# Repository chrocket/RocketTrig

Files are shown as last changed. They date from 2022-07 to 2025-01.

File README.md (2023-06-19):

# RocketTrig
A camera controller for photographing high poweed model rockets


This is a camera controller. Each "node" contains outputs to control one or two cameras.  Camera nodes can communicate to each others over an RF link. Two nodes make up a system, say one at the flight line and one up close to the rocket. Liftoffs can be triggered by a variety of sensors to detect lift-off, or manually via a foot switch.

Schematic, BOM, JLBPCB files and firmware are all included.
Note:  Even those some files are labelled "CameraTriggerSensorNodeOnly" they are really Camera nodes.

This is based on the Adafruit Feather M0 LoRa board (Adafruit 3178). It also works with RFM65 radio version of that board, cheaper but less range (Adafruit 3176). There is a #define to select between the two, and the frequency of operation will have to be in the range of the chip.

To build firmware, you will need Arduino IDE. I'm using ver 1.8.19.  You will need to set up the Adafruit boards in the boards manager (Add https://adafruit.github.io/arduino-board-index/package_adafruit_index.json to Additional boards URL under Preferences).  Set "Adafruit Feather M0 (SAMD21)" Under Tools/Board.

I'm using dependencies (under library manager):
CRC32 by Christopher Baker  https://github.com/bakercp/CRC32/blob/master/examples/CRC32/CRC32.ino
Requires RadioHead libs
// https://www.airspayce.com/mikem/arduino/RadioHead/index.html
// Download from Adafruit https://cdn-learn.adafruit.com/assets/assets/000/035/106/original/RadioHead-1.62.zip?1472068723
CCW MorseTX
https://github.com/ridencww/cww_MorseTx

You will likely want to change the default 915.35 MHz operating frequency. This is done by a #define.  This will deconfict different users who might want to simultaneously use the sytem.

--------------------------------------------------------------------------------------------------------------
In June 2023, I had Eureka moment. I realized that with virtuallly no changes, the RocketTrig board could be used as a wireless Launch controller and still trigger cameras.  I modified the program to work with this and later worked up a separate board "Rev 4_1" that could better meet both remote launch and remote camera trigger functions.

(Remote launch can still trigger cameras both local and remote)

Here is the Rev 4_1 board
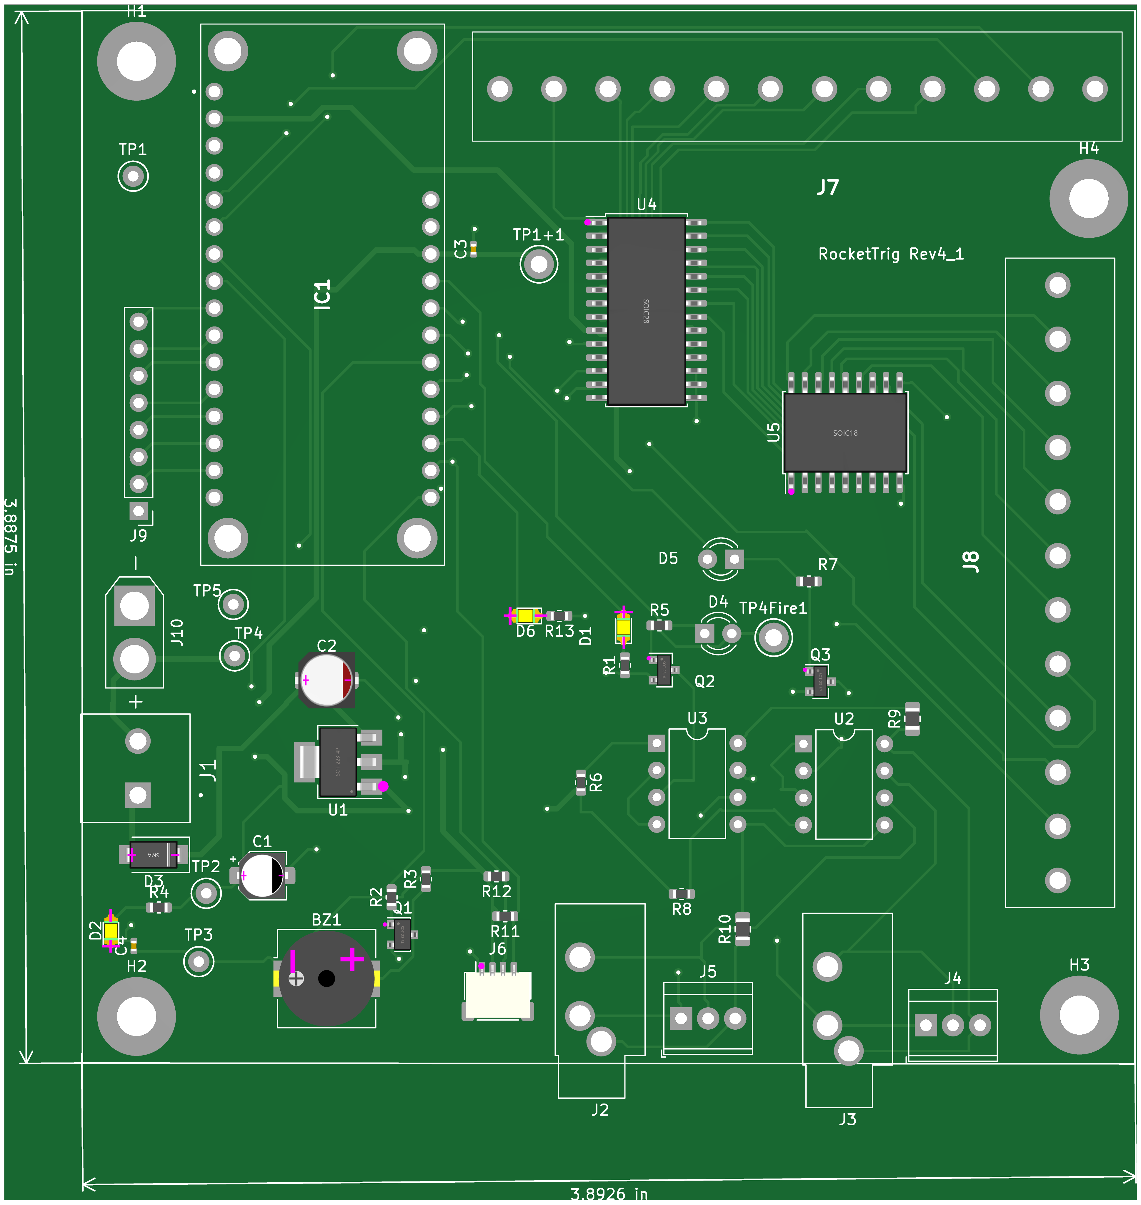
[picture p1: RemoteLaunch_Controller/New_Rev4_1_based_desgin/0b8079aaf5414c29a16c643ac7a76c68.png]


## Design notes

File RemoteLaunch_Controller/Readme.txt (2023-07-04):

Uses the CameraTrig board, as-is to create a wireless launch capability.

(Some pins for sensors are needed for a relay and LED).

Camera will trigger when "launch" is fired (for a two second "on")

Poll button becomes "clear", "Arm" is still "Arm" and "Trigger" becomes launch.

Press "Arm", which will arm system, after 15 sec, it will time out.
- Will also go to disarm, if you hit "clear"
- Will disarm after a launch.

After system is in "arm", hit "launch" to fire the ignitors in the remote box for 2s
- Hitting "clear" will turn off ignitors, if still in the 2 s window

Schematics enclosed for external board connections, as well as BOM.

***********************************************
NOTE  Variations
***********************************************
RocketTrig_based_board  is based on the orinal board   6/2023

CameraTriggerRev 4_2 w Launch Controller 2023  is a re-do with i2c i/o expander and darlington driver array  7/2023
4ChWirelessLaunchController - try 2 w relay pcb - is a relay board for Rev 4_2  7/2023

***********************************************
NOTE  Migrated to Kicad 7
***********************************************

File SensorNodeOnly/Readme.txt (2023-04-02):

Sensor Node only board

Supports a variety of sensors

Used with jlcpcb pc board fab

This is not stand-alone;  must be used in concert with at least on RocketTrig Node.

Edit Camera_reomote_txrx_sensorNodeOnly.ino
- Select one sensor type only (Sensor_x) and re-compile
- Set behvior of overrideAlwaysArmed
      True - a sensor hit will always trigger camear
      False - a sensor hit will only trigger camera if "armed" is true (use this for sensors with lots of false positives, but you must arm before you are ready to take a picture)

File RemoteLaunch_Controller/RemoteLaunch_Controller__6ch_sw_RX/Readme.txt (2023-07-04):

Ardino code for RocketTrig based board.

Separate code for 4_2 revision.

https://learn.adafruit.com/adafruit-feather-m4-express-atsamd51/adapting-sketches-to-m0

Fixes from Rev 4_1
Regulator U1 chip has wrong footprint
D6 has incorrext part
BZ1 soldered on backwards.

TODO fixes for Rev 4_2
Thicker traces between U4 and U5

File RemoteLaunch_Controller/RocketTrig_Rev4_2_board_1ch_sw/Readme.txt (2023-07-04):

This is based on the orignial RocketTrig board.

I subsquently redesigned the board "Revision 4_1" to make it more cross compatiable with camera trigger use case and remote launch use case.

Arduino IDE 2.1.0 setup
https://learn.adafruit.com/adafruit-feather-m0-basic-proto/setup
Board is "Adafruit Feather M0 (SAMD21)"

https://learn.adafruit.com/adafruit-feather-m0-basic-proto/using-with-arduino-ide

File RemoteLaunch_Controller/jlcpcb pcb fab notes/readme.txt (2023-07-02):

Export producution outputs to JLCPCB:

https://support.jlcpcb.com/article/149-how-to-generate-gerber-and-drill-files-in-kicad

Generate BOM:
https://support.jlcpcb.com/article/84-how-to-generate-the-bom-and-centroid-file-from-kicad
- Create xml file
- Download   https://gist.github.com/arturo182/a8c4a4b96907cfccf616a1edb59d0389
- Use online xslt converter https://freeformatter.com/xsl-transformer.html

Generating Pick and Place files
The CPL file has to be generated from the PCB editor, click on File -> Fabrication output -> Footprint position (.pos) file 

The folling changes are required:

Ref to Designator PosX to Mid X PosY to Mid Y Rot to Rotation Side to Layer

Before, as exported from KiCAD:

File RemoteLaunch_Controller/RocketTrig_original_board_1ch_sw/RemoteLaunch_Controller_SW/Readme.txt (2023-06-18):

Ardino code for RocketTrig based board.

Separate code for 4_1 revision.

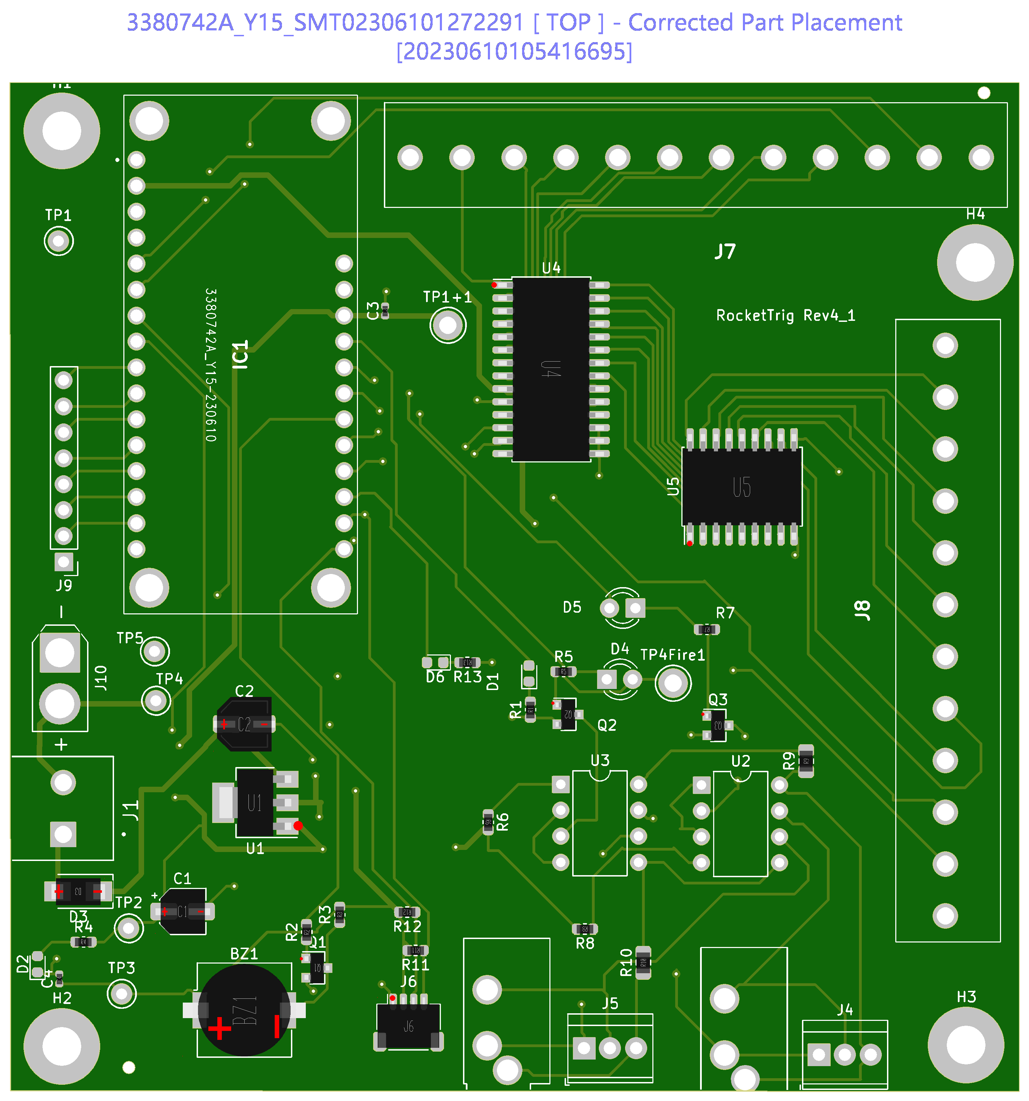
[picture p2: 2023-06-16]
downloadSmtDFMPatchImg.png

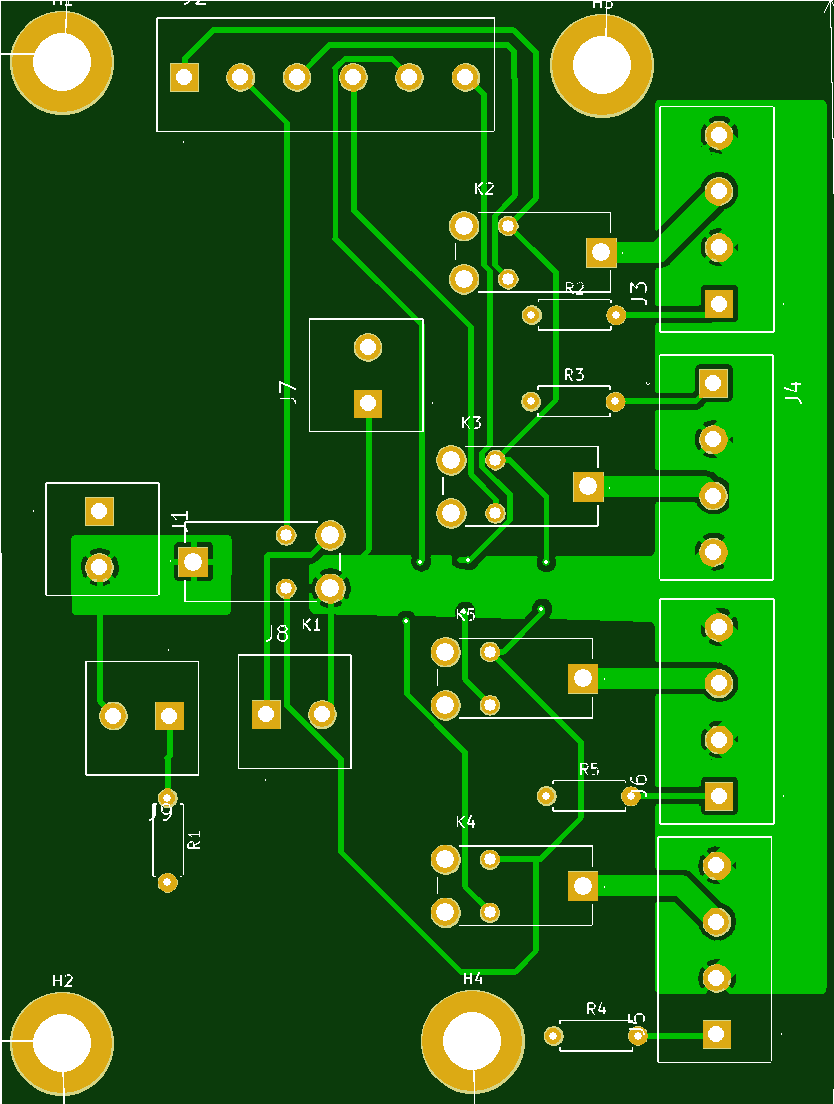
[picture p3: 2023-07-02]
RemoteLaunch_Controller/4ChWirelessLaunchController - try 2 w relay pcb/relayBoard.png

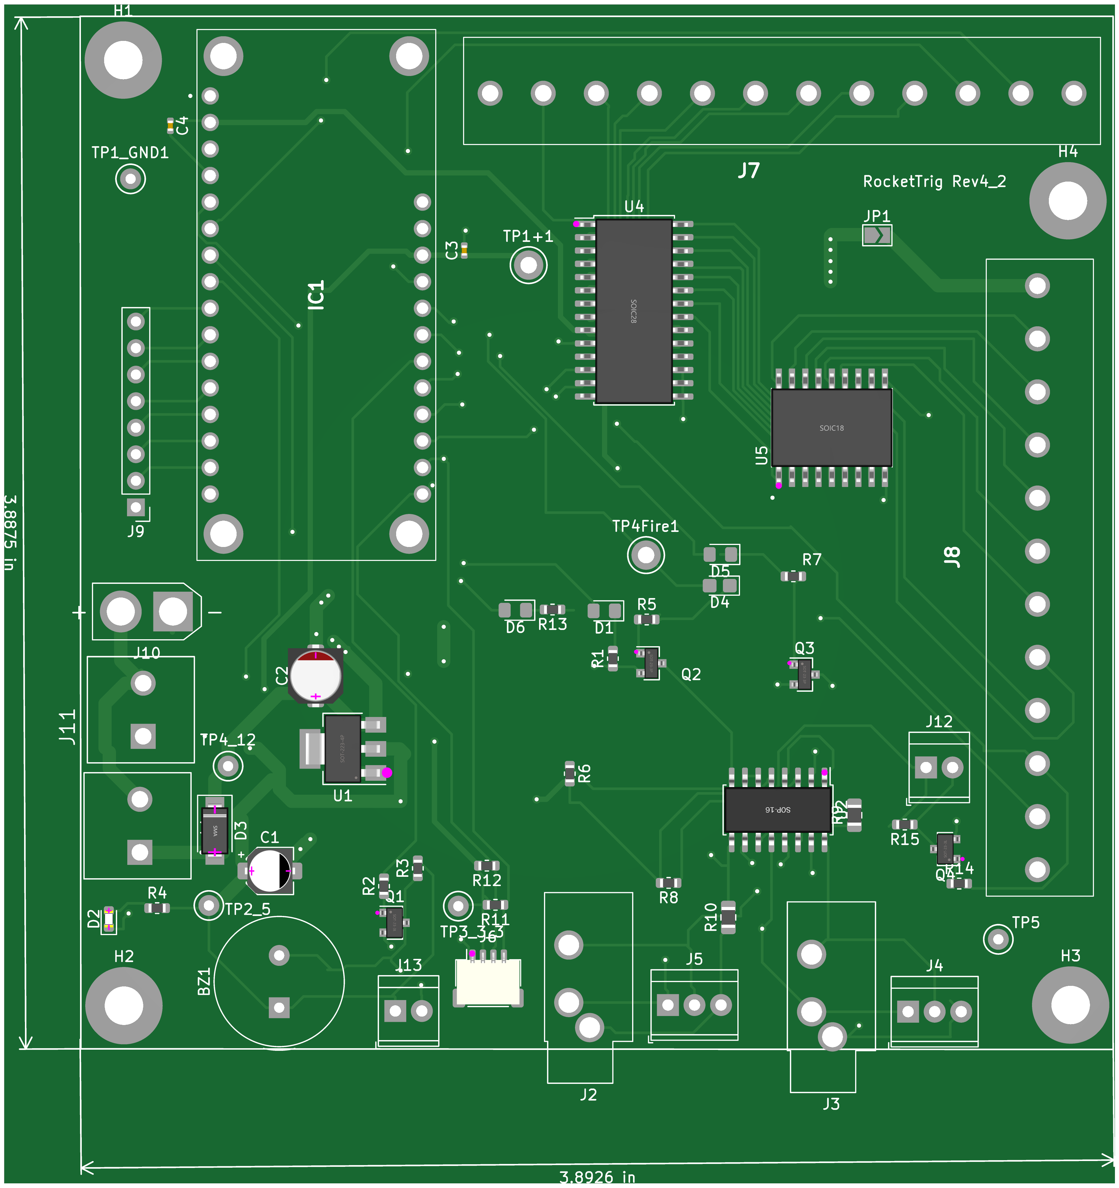
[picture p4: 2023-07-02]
RemoteLaunch_Controller/CameraTriggerRev 4_3 w Launch Controller 2023/rev4_2 board.png

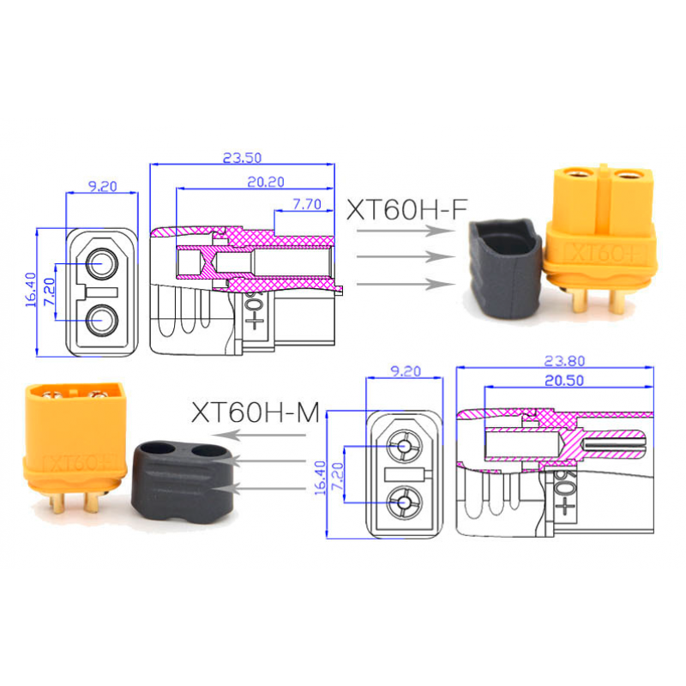
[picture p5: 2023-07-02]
RemoteLaunch_Controller/Datasheets/amass-xt60h-connector-male-female-60a-current.png

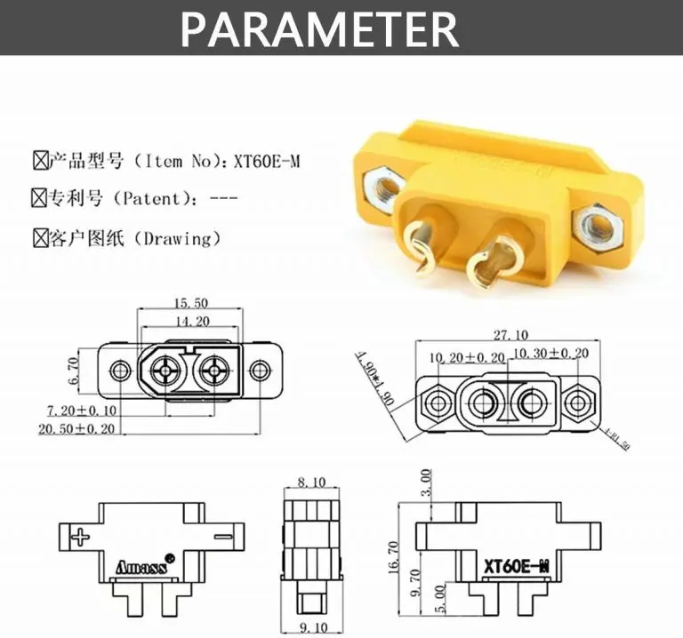
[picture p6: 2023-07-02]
RemoteLaunch_Controller/Datasheets/XT60E-M_003-768x718.webp

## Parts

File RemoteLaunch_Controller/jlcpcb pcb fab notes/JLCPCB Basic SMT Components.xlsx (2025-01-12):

Library Type | Component Number | Component Name | Package Specification | Component Category | Component Provider | Quantity In Stock | Price | Manufacturer Model Number | Brand | Sales Statistics | Comments
Basic Library | C78395 | P6SMB6.8CA | SMB,DO-214AA | Diode _TVS Diode | Provided by Jiali Chuang | 44428 | Click to view | P6SMB6.8CA | BRIGHTKING å °æ¹¾å ›è€€ | Very popular | Basic Library
Basic Library | C2286 | Red Light | LED_0603 | Diode_LED | Provided by Jiali Chuang | 487769 | Click to view | Red Light 0603 | KENTO | Very popular | LED,LED,LED
Basic Library | C2297 | Green | LED_0805 | Diode_LED | Provided by Jiali Chuang | 242210 | Click to view | 0805G (Green) | KENTO | Very popular
Basic Library | C4211 | 3KÎ© (3001) Â±1% | 603 | Resistor_chip resistor | Provided by Jiali Chuang | 333157 | Click to view | 0603WAF3001T5E | UNIOHMå °æ¹¾åŽšå£° | Very popular
Basic Library | C32346 | 32.768KHZ Â±20PPM 12.5PF | SMD-3215_2P | Crystal _ patch passive crystal | Provided by Jiali Chuang | 59158 | Click to view | Q13FC1350000400 | EPSON çˆ±æ™®ç”Ÿ | Very popular
Basic Library | C8963 | SP3485EN-L/TR | SOIC-8_150MIL | RS-485/RS-422 | Provided by Jiali Chuang | 16598 | Click to view | SP3485EN-L/TR | EXAR è‰¾ç§‘å˜‰ | Very popular
Basic Library | C1779 | 4.7UF (475) Â±10% 25V X5R | 805 | Capacitor_chip capacitor | Provided by Jiali Chuang | 340020 | Click to view | CL21A475KAQNNNE | SAMSUNG ä¸‰æ˜Ÿ | Very popular
Basic Library | C23182 | 47Î© (47R0) Â±1% | 603 | Resistor_chip resistor | Provided by Jiali Chuang | 170507 | Click to view | 0603WAF470JT5E | UNIOHMå °æ¹¾åŽšå£° | Very popular
Basic Library | C25900 | 4.7KÎ© (4701) Â±1% | 402 | Resistor_chip resistor | Provided by Jiali Chuang | 526356 | Click to view | 0402WGF4701TCE | UNIOHMå °æ¹¾åŽšå£° | Very popular
Basic Library | C25792 | 47KÎ© (4702) Â±1% | 402 | Resistor_chip resistor | Provided by Jiali Chuang | 93727 | Click to view | 0402WGF4702TCE | UNIOHMå °æ¹¾åŽšå£° | Very popular
Basic Library | C2145 | MMBT5551 G1 | SOT-23 | Transistor | Provided by Jiali Chuang | 771675 | Click to view | MMBT5551 | CJæ±Ÿè‹ é•¿ç”µ | Very popular
Basic Library | C23231 | 68KÎ© (6802) Â±1% | 603 | Resistor_chip resistor | Provided by Jiali Chuang | 58006 | Click to view | 0603WAF6802T5E | UNIOHMå °æ¹¾åŽšå£° | Very popular
Basic Library | C21189 | 0Î© (0R0) Â±1% | 603 | Resistor_chip resistor | Provided by Jiali Chuang | 898614 | Click to view | 0603WAF0000T5E | UNIOHMå °æ¹¾åŽšå£° | Very popular
Basic Library | C1644 | 15PF (150) Â±5% 50V C0G | 603 | Capacitor_chip capacitor | Provided by Jiali Chuang | 124557 | Click to view | CL10C150JB8NNNC | SAMSUNG ä¸‰æ˜Ÿ | Very popular
Basic Library | C1798 | 20PF (200) Â±5% 50V C0G | 805 | Capacitor_chip capacitor | Provided by Jiali Chuang | 82284 | Click to view | CL21C200JBANNNC | SAMSUNG ä¸‰æ˜Ÿ | Very popular
Basic Library | C1588 | 1NF (102) Â±10% 50V X7R | 603 | Capacitor_chip capacitor | Provided by Jiali Chuang | 332197 | Click to view | CL10B102KB8NNNC | SAMSUNG ä¸‰æ˜Ÿ | Very popular
Basic Library | C1613 | 3.3NF (332) Â±10% 50V X7R | 603 | Capacitor_chip capacitor | Provided by Jiali Chuang | 68884 | Click to view | CL10B332KB8NNNC | SAMSUNG ä¸‰æ˜Ÿ | Very popular
Basic Library | C1710 | 10NF (103) Â±10% 50V X7R | 805 | Capacitor_chip capacitor | Provided by Jiali Chuang | 443415 | Click to view | CL21B103KBANNNC | SAMSUNG ä¸‰æ˜Ÿ | Very popular
Basic Library | C1622 | 47NF (473) Â±10% 50V X7R | 603 | Capacitor_chip capacitor | Provided by Jiali Chuang | 158108 | Click to view | CL10B473KB8NNNC | SAMSUNG ä¸‰æ˜Ÿ | Very popular
Basic Library | C1623 | 470NF (474) Â±10% 25V X7R | 603 | Capacitor_chip capacitor | Provided by Jiali Chuang | 78149 | Click to view | CL10B474KA8NNNC | SAMSUNG ä¸‰æ˜Ÿ | Very popular
Basic Library | C28323 | 1UF (105) Â±10% 50V X7R | 805 | Capacitor_chip capacitor | Provided by Jiali Chuang | 426328 | Click to view | CL21B105KBFNNNE | SAMSUNG ä¸‰æ˜Ÿ | Very popular
Basic Library | C25077 | 10Î© (10R0) Â±1% | 402 | Resistor_chip resistor | Provided by Jiali Chuang | 31991 | Click to view | 0402WGF100JTCE | UNIOHMå °æ¹¾åŽšå£° | Very popular
Basic Library | C17513 | 1KÎ© (1001) Â±1% | 805 | Resistor_chip resistor | Provided by Jiali Chuang | 1610820 | Click to view | 0805W8F1001T5E | UNIOHMå °æ¹¾åŽšå£° | Very popular
Basic Library | C17514 | 1MÎ© (1004) Â±1% | 805 | Resistor_chip resistor | Provided by Jiali Chuang | 161367 | Click to view | 0805W8F1004T5E | UNIOHMå °æ¹¾åŽšå£° | Very popular
Basic Library | C17437 | 120Î© (1200) Â±1% | 805 | Resistor_chip resistor | Provided by Jiali Chuang | 111132 | Click to view | 0805W8F1200T5E | UNIOHMå °æ¹¾åŽšå£° | Very popular
Basic Library | C9002 | 12MHZ 20PF 10PPM | SMD-3225_4P | Crystal _ patch passive crystal | Provided by Jiali Chuang | 41017 | Click to view | X322512MSB4SI | LC ç«‹åˆ› | Very popular | Crystal Oscillator
Basic Library | C4310 | 1.5KÎ© (1501) Â±1% | 805 | Resistor_chip resistor | Provided by Jiali Chuang | 112854 | Click to view | 0805W8F1501T5E | UNIOHMå °æ¹¾åŽšå£° | Very popular
Basic Library | C22843 | 1.5KÎ© (1501) Â±1% | 603 | Resistor_chip resistor | Provided by Jiali Chuang | 230744 | Click to view | 0603WAF1501T5E | UNIOHMå °æ¹¾åŽšå£° | Very popular
Basic Library | C8218 | 200Î© (2000) Â±1% | 603 | Resistor_chip resistor | Provided by Jiali Chuang | 234580 | Click to view | 0603WAF2000T5E | UNIOHMå °æ¹¾åŽšå£° | Very popular
Basic Library | C4184 | 20KÎ© (2002) Â±1% | 603 | Resistor_chip resistor | Provided by Jiali Chuang | 623888 | Click to view | 0603WAF2002T5E | UNIOHMå °æ¹¾åŽšå£° | Very popular
Basic Library | C31850 | 22KÎ© (2202) Â±1% | 603 | Resistor_chip resistor | Provided by Jiali Chuang | 217681 | Click to view | 0603WAF2202T5E | UNIOHMå °æ¹¾åŽšå£° | Very popular
Basic Library | C23140 | 33Î© (33R0) Â±1% | 603 | Resistor_chip resistor | Provided by Jiali Chuang | 360971 | Click to view | 0603WAF330JT5E | UNIOHMå °æ¹¾åŽšå£° | Very popular
Basic Library | C4216 | 33KÎ© (3302) Â±1% | 603 | Resistor_chip resistor | Provided by Jiali Chuang | 155297 | Click to view | 0603WAF3302T5E | UNIOHMå °æ¹¾åŽšå£° | Very popular
Basic Library | C23179 | 470Î© (4700) Â±1% | 603 | Resistor_chip resistor | Provided by Jiali Chuang | 642856 | Click to view | 0603WAF4700T5E | UNIOHMå °æ¹¾åŽšå£° | Very popular
Basic Library | C23186 | 5.1KÎ© (5101) Â±1% | 603 | Resistor_chip resistor | Provided by Jiali Chuang | 1120756 | Click to view | 0603WAF5101T5E | UNIOHMå °æ¹¾åŽšå£° | Very popular
Basic Library | C7950 | LM358DR2G | SOIC-8_150MIL | Op Amp_General Op Amp | Provided by Jiali Chuang | 26389 | Click to view | LM358DR2G | ON å®‰æ£®ç¾Ž | Very popular
Basic Library | C2480 | SS14 | SMA,DO-214AC | Diode_Schottky diode | Provided by Jiali Chuang | 131758 | Click to view | SS14 | MDD | Very popular | SMT Phase IV - Extended Library
Basic Library | C8323 | STM32F103RCT6 | LQFP-64_10X10X05P | Microcontroller (MCU) | Provided by Jiali Chuang | 8995 | Click to view | STM32F103RCT6 | ST æ„ æ³•å Šå¯¼ä½“ | Very popular
Basic Library | C1804 | 22PF (220) Â±5% 50V C0G | 805 | Capacitor_chip capacitor | Provided by Jiali Chuang | 154977 | Click to view | CL21C220JBANNNC | SAMSUNG ä¸‰æ˜Ÿ | Very popular
Basic Library | C1663 | 33PF (330) Â±5% 50V C0G | 603 | Capacitor_chip capacitor | Provided by Jiali Chuang | 168388 | Click to view | CL10C330JB8NNNC | SAMSUNG ä¸‰æ˜Ÿ | Very popular
Basic Library | C1620 | 470PF (471) Â±10% 50V X7R | 603 | Capacitor_chip capacitor | Provided by Jiali Chuang | 134164 | Click to view | 0603B471K500NT | FH é£Žå Ž | Very popular
Basic Library | C15195 | 10NF (103) Â±10% 50V X7R | 402 | Capacitor_chip capacitor | Provided by Jiali Chuang | 188177 | Click to view | CL05B103KB5NNNC | SAMSUNG ä¸‰æ˜Ÿ | Very popular
Basic Library | C1525 | 100NF (104) Â±10% 16V X7R | 402 | Capacitor_chip capacitor | Provided by Jiali Chuang | 2523762 | Click to view | CL05B104KO5NNNC | SAMSUNG ä¸‰æ˜Ÿ | Very popular
Basic Library | C15849 | 1UF (105) Â±10% 50V X5R | 603 | Capacitor_chip capacitor | Provided by Jiali Chuang | 808121 | Click to view | CL10A105KB8NNNC | SAMSUNG ä¸‰æ˜Ÿ | Very popular
Basic Library | C15850 | 10UF (106) Â±10% 25V X5R | 805 | Capacitor_chip capacitor | Provided by Jiali Chuang | 898972 | Click to view | CL21A106KAYNNNE | SAMSUNG ä¸‰æ˜Ÿ | Very popular
Basic Library | C25076 | 100Î© (1000) Â±1% | 402 | Resistor_chip resistor | Provided by Jiali Chuang | 39332 | Click to view | 0402WGF1000TCE | UNIOHMå °æ¹¾åŽšå£° | Very popular
Basic Library | C17901 | 100Î© (1000) Â±1% | 1206 | Resistor_chip resistor | Provided by Jiali Chuang | 119831 | Click to view | 1206W4F1000T5E | UNIOHMå °æ¹¾åŽšå£° | Very popular
Basic Library | C21190 | 1KÎ© (1001) Â±1% | 603 | Resistor_chip resistor | Provided by Jiali Chuang | 3803116 | Click to view | 0603WAF1001T5E | UNIOHMå °æ¹¾åŽšå£° | Very popular
Basic Library | C4410 | 1KÎ© (1001) Â±1% | 1206 | Resistor_chip resistor | Provided by Jiali Chuang | 292944 | Click to view | 1206W4F1001T5E | UNIOHMå °æ¹¾åŽšå£° | Very popular
Basic Library | C17414 | 10KÎ© (1002) Â±1% | 805 | Resistor_chip resistor | Provided by Jiali Chuang | 5522740 | Click to view | 0805W8F1002T5E | UNIOHMå °æ¹¾åŽšå£° | Very popular
Basic Library | C22809 | 15KÎ© (1502) Â±1% | 603 | Resistor_chip resistor | Provided by Jiali Chuang | 123104 | Click to view | 0603WAF1502T5E | UNIOHMå °æ¹¾åŽšå£° | Very popular
Basic Library | C2128 | 1N4148WS T4 | SOD-323 | Diode_switching diode | Provided by Jiali Chuang | 708056 | Click to view | 1N4148 | CJæ±Ÿè‹ é•¿ç”µ | Very popular
Basic Library | C25811 | 200KÎ© (2003) Â±1% | 603 | Resistor_chip resistor | Provided by Jiali Chuang | 194667 | Click to view | 0603WAF2003T5E | UNIOHMå °æ¹¾åŽšå£° | Very popular
Basic Library | C23345 | 22Î© (22R0) Â±1% | 603 | Resistor_chip resistor | Provided by Jiali Chuang | 484768 | Click to view | 0603WAF220JT5E | UNIOHMå °æ¹¾åŽšå£° | Very popular
Basic Library | C4190 | 2.2KÎ© (2201) Â±1% | 603 | Resistor_chip resistor | Provided by Jiali Chuang | 487166 | Click to view | 0603WAF2201T5E | UNIOHMå °æ¹¾åŽšå£° | Very popular
Basic Library | C13167 | 2.7KÎ© (2701) Â±1% | 603 | Resistor_chip resistor | Provided by Jiali Chuang | 85676 | Click to view | 0603WAF2701T5E | UNIOHMå °æ¹¾åŽšå£° | Very popular
Basic Library | C22967 | 27KÎ© (2702) Â±1% | 603 | Resistor_chip resistor | Provided by Jiali Chuang | 8032 | Click to view | 0603WAF2702T5E | UNIOHMå °æ¹¾åŽšå£° | Very popular
Basic Library | C8545 | 2N7002 | SOT-23 | MOS_FET | Provided by Jiali Chuang | 100556 | Click to view | 2N7002 | CJæ±Ÿè‹ é•¿ç”µ | Very popular
Basic Library | C58069 | L78M05ABDT-TR | TO-252-2 | LDO_ low dropout linear regulator | Provided by Jiali Chuang | 36244 | Click to view | L78M05ABDT-TR | ST æ„ æ³•å Šå¯¼ä½“ | Very popular
Basic Library | C17661 | 3KÎ© (3001) Â±1% | 805 | Resistor_chip resistor | Provided by Jiali Chuang | 130844 | Click to view | 0805W8F3001T5E | UNIOHMå °æ¹¾åŽšå£° | Very popular
Basic Library | C22984 | 30KÎ© (3002) Â±1% | 603 | Resistor_chip resistor | Provided by Jiali Chuang | 144691 | Click to view | 0603WAF3002T5E | UNIOHMå °æ¹¾åŽšå£° | Very popular
Basic Library | C23138 | 330Î© (3300) Â±1% | 603 | Resistor_chip resistor | Provided by Jiali Chuang | 170059 | Click to view | 0603WAF3300T5E | UNIOHMå °æ¹¾åŽšå£° | Very popular
Basic Library | C19666 | 4.7UF (475) Â±10% 16V X5R | 603 | Capacitor_chip capacitor | Provided by Jiali Chuang | 164217 | Click to view | CL10A475KO8NNNC | SAMSUNG ä¸‰æ˜Ÿ | Very popular
Basic Library | C29823 | 4.7UF (475) Â±10% 50V X7R | 1206 | Capacitor_chip capacitor | Provided by Jiali Chuang | 80189 | Click to view | 1206B475K500NT | FH é£Žå Ž | Very popular
Basic Library | C23162 | 4.7KÎ© (4701) Â±1% | 603 | Resistor_chip resistor | Provided by Jiali Chuang | 1737223 | Click to view | 0603WAF4701T5E | UNIOHMå °æ¹¾åŽšå£° | Very popular
Basic Library | C17673 | 4.7KÎ© (4701) Â±1% | 805 | Resistor_chip resistor | Provided by Jiali Chuang | 1972685 | Click to view | 0805W8F4701T5E | UNIOHMå °æ¹¾åŽšå£° | Very popular
Basic Library | C25819 | 47KÎ© (4702) Â±1% | 603 | Resistor_chip resistor | Provided by Jiali Chuang | 387305 | Click to view | 0603WAF4702T5E | UNIOHMå °æ¹¾åŽšå£° | Very popular
Basic Library | C17713 | 47KÎ© (4702) Â±1% | 805 | Resistor_chip resistor | Provided by Jiali Chuang | 140146 | Click to view | 0805W8F4702T5E | UNIOHMå °æ¹¾åŽšå£° | Very popular
Basic Library | C23178 | 470KÎ© (4703) Â±1% | 603 | Resistor_chip resistor | Provided by Jiali Chuang | 57898 | Click to view | 0603WAF4703T5E | UNIOHMå °æ¹¾åŽšå£° | Very popular
Basic Library | C23185 | 49.9Î© (49R9) Â±1% | 603 | Resistor_chip resistor | Provided by Jiali Chuang | 150812 | Click to view | 0603WAF499JT5E | UNIOHMå °æ¹¾åŽšå£° | Very popular
Basic Library | C23189 | 5.6KÎ© (5601) Â±1% | 603 | Resistor_chip resistor | Provided by Jiali Chuang | 146579 | Click to view | 0603WAF5601T5E | UNIOHMå °æ¹¾åŽšå£° | Very popular
Basic Library | C23228 | 680Î© (6800) Â±1% | 603 | Resistor_chip resistor | Provided by Jiali Chuang | 156091 | Click to view | 0603WAF6800T5E | UNIOHMå °æ¹¾åŽšå£° | Very popular
Basic Library | C23212 | 6.8KÎ© (6801) Â±1% | 603 | Resistor_chip resistor | Provided by Jiali Chuang | 114673 | Click to view | 0603WAF6801T5E | UNIOHMå °æ¹¾åŽšå£° | Very popular
Basic Library | C115962 | YSX530GA 8MHZ 20PF 10PPM | SMD-5032_2P | Crystal _ patch passive crystal | Provided by Jiali Chuang | 102629 | Click to view | X50328MSB2GI | YXC | Very popular
Basic Library | C6749 | S9013 J3 | SOT-23 | Transistor | Provided by Jiali Chuang | 82122 | Click to view | S9013 | CJæ±Ÿè‹ é•¿ç”µ | Very popular
Basic Library | C17477 | 0Î© (0R0) Â±1% | 805 | Resistor_chip resistor | Provided by Jiali Chuang | 687407 | Click to view | 0805W8F0000T5E | UNIOHMå °æ¹¾åŽšå£° | Very popular
Basic Library | C1653 | 22PF (220) Â±5% 50V C0G | 603 | Capacitor_chip capacitor | Provided by Jiali Chuang | 195181 | Click to view | CL10C220JB8NNNC | SAMSUNG ä¸‰æ˜Ÿ | Very popular
Basic Library | C1671 | 47PF (470) Â±5% 50V C0G | 603 | Capacitor_chip capacitor | Provided by Jiali Chuang | 114824 | Click to view | CL10C470JB8NNNC | SAMSUNG ä¸‰æ˜Ÿ | Very popular
Basic Library | C14858 | 100PF (101) Â±5% 50V C0G | 603 | Capacitor_chip capacitor | Provided by Jiali Chuang | 233875 | Click to view | CL10C101JB8NNNC | SAMSUNG ä¸‰æ˜Ÿ | Very popular
Basic Library | C1848 | 1UF (105) Â±10% 50V X7R | 1206 | Capacitor_chip capacitor | Provided by Jiali Chuang | 63859 | Click to view | CL31B105KBHNNNE | SAMSUNG ä¸‰æ˜Ÿ | Very popular
Basic Library | C22775 | 100Î© (1000) Â±1% | 603 | Resistor_chip resistor | Provided by Jiali Chuang | 1562883 | Click to view | 0603WAF1000T5E | UNIOHMå °æ¹¾åŽšå£° | Very popular
Basic Library | C11702 | 1KÎ© (1001) Â±1% | 402 | Resistor_chip resistor | Provided by Jiali Chuang | 577122 | Click to view | 0402WGF1001TCE | UNIOHMå °æ¹¾åŽšå£° | Very popular
Basic Library | C29718 | 10KÎ© (103) Â±5% | 0603_X4 | Resistor_chip exclusion | Provided by Jiali Chuang | 130842 | Click to view | 4D03WGJ0103T5E | UNIOHMå °æ¹¾åŽšå£° | Very popular
Basic Library | C25741 | 100KÎ© (1003) Â±1% | 402 | Resistor_chip resistor | Provided by Jiali Chuang | 1230997 | Click to view | 0402WGF1003TCE | UNIOHMå °æ¹¾åŽšå£° | Very popular
Basic Library | C22935 | 1MÎ© (1004) Â±1% | 603 | Resistor_chip resistor | Provided by Jiali Chuang | 176852 | Click to view | 0603WAF1004T5E | UNIOHMå °æ¹¾åŽšå£° | Very popular
Basic Library | C6186 | AMS1117-3.3 | SOT-223 | LDO_ low dropout linear regulator | Provided by Jiali Chuang | 143229 | Click to view | AMS1117-3.3 | ç¾Žå›½AMS | Very popular
Basic Library | C22765 | 1.2KÎ© (1201) Â±1% | 603 | Resistor_chip resistor | Provided by Jiali Chuang | 82595 | Click to view | 0603WAF1201T5E | UNIOHMå °æ¹¾åŽšå£° | Very popular
Basic Library | C22790 | 12KÎ© (1202) Â±1% | 603 | Resistor_chip resistor | Provided by Jiali Chuang | 132016 | Click to view | 0603WAF1202T5E | UNIOHMå °æ¹¾åŽšå£° | Very popular
Basic Library | C17475 | 15KÎ© (1502) Â±1% | 805 | Resistor_chip resistor | Provided by Jiali Chuang | 48506 | Click to view | 0805W8F1502T5E | UNIOHMå °æ¹¾åŽšå£° | Very popular
Basic Library | C81598 | 1N4148W | SOD-123 | Diode_switching diode | Provided by Jiali Chuang | 457242 | Click to view | 1N4148W | ST å…ˆç§‘ | Very popular
Basic Library | C49217 | 2.2UF (225) Â±20% 50V Y5V | 805 | Capacitor_chip capacitor | Provided by Jiali Chuang | 117671 | Click to view | 0805F225M500NT | FH é£Žå Ž | Very popular
Basic Library | C17540 | 200Î© (2000) Â±1% | 805 | Resistor_chip resistor | Provided by Jiali Chuang | 242406 | Click to view | 0805W8F2000T5E | UNIOHMå °æ¹¾åŽšå£° | Very popular
Basic Library | C22975 | 2KÎ© (2001) Â±1% | 603 | Resistor_chip resistor | Provided by Jiali Chuang | 449533 | Click to view | 0603WAF2001T5E | UNIOHMå °æ¹¾åŽšå£° | Very popular
Basic Library | C25765 | 20KÎ© (2002) Â±1% | 402 | Resistor_chip resistor | Provided by Jiali Chuang | 192804 | Click to view | 0402WGF2002TCE | UNIOHMå °æ¹¾åŽšå£° | Very popular
Basic Library | C23352 | 24KÎ© (2402) Â±1% | 603 | Resistor_chip resistor | Provided by Jiali Chuang | 110129 | Click to view | 0603WAF2402T5E | UNIOHMå °æ¹¾åŽšå£° | Very popular
Basic Library | C2150 | SS8050 | SOT-23 | Transistor | Provided by Jiali Chuang | 946378 | Click to view | SS8050 | CJæ±Ÿè‹ é•¿ç”µ | Very popular | SS8050 Y1
Basic Library | C72038 | Yellow Light | LED_0603 | Diode_LED | Provided by Jiali Chuang | 180102 | Click to view | 19-213/Y2C-CQ2R2L/3T(CY) | EVERLIGHT å °æ¹¾äº¿å…‰ | Very popular | LED,LED,LED
Basic Library | C7512 | ULN2003ADR | SOIC-16_150MIL | High Current Driver | Provided by Jiali Chuang | 36824 | Click to view | ULN2003ADR | TI å¾·å·žä»ªå™¨ | Very popular
Basic Library | C84256 | Red Light è´´ç‰‡LED | LED_0805 | Diode_LED | Provided by Jiali Chuang | 637632 | Click to view | FC-2012HRK-620D | å›½æ˜Ÿå…‰ç”µ | Very popular
Basic Library | C20526 | MMBT3904 1AM 100-300 | SOT-23 | Transistor | Provided by Jiali Chuang | 68468 | Click to view | MMBT3904 | CJæ±Ÿè‹ é•¿ç”µ | Very popular | 2N3904
Basic Library | C17630 | 330Î© (3300) Â±1% | 805 | Resistor_chip resistor | Provided by Jiali Chuang | 352712 | Click to view | 0805W8F3300T5E | UNIOHMå °æ¹¾åŽšå£° | Very popular
Basic Library | C26010 | 3.3KÎ© (3301) Â±1% | 805 | Resistor_chip resistor | Provided by Jiali Chuang | 288025 | Click to view | 0805W8F3301T5E | UNIOHMå °æ¹¾åŽšå£° | Very popular
Basic Library | C20917 | AO3400A Né “æ²Ÿ X0YV1T SOT-23 | SOT-23-3L | MOS_FET | Provided by Jiali Chuang | 123039 | Click to view | AO3400A | AOS | Very popular
Basic Library | C6855 | SP485EEN-L/TR | SOIC-8_150MIL | RS-485/RS-422 | Provided by Jiali Chuang | 27518 | Click to view | SP485EEN-L/TR | EXAR è‰¾ç§‘å˜‰ | Very popular
Basic Library | C23197 | 51Î© (51R0) Â±1% | 603 | Resistor_chip resistor | Provided by Jiali Chuang | 118963 | Click to view | 0603WAF510JT5E | UNIOHMå °æ¹¾åŽšå£° | Very popular
Basic Library | C17734 | 510Î© (5100) Â±1% | 805 | Resistor_chip resistor | Provided by Jiali Chuang | 321248 | Click to view | 0805W8F5100T5E | UNIOHMå °æ¹¾åŽšå£° | Very popular
Basic Library | C23196 | 51KÎ© (5102) Â±1% | 603 | Resistor_chip resistor | Provided by Jiali Chuang | 217597 | Click to view | 0603WAF5102T5E | UNIOHMå °æ¹¾åŽšå£° | Very popular
Basic Library | C8598 | B5819W SL | SOD-123 | Diode_Schottky diode | Provided by Jiali Chuang | 136634 | Click to view | B5819W | CJæ±Ÿè‹ é•¿ç”µ | Very popular
Basic Library | C17168 | 0Î© (0R0) Â±1% | 402 | Resistor_chip resistor | Provided by Jiali Chuang | 298947 | Click to view | 0402WGF0000TCE | UNIOHMå °æ¹¾åŽšå£° | Very popular
Basic Library | C1634 | 10PF (100) Â±5% 50V C0G | 603 | Capacitor_chip capacitor | Provided by Jiali Chuang | 174504 | Click to view | CL10C100JB8NNNC | SAMSUNG ä¸‰æ˜Ÿ | Very popular
Basic Library | C1648 | 20PF (200) Â±5% 50V C0G | 603 | Capacitor_chip capacitor | Provided by Jiali Chuang | 287882 | Click to view | CL10C200JB8NNNC | SAMSUNG ä¸‰æ˜Ÿ | Very popular
Basic Library | C1790 | 100PF (101) Â±5% 50V C0G | 805 | Capacitor_chip capacitor | Provided by Jiali Chuang | 161189 | Click to view | CL21C101JBANNNC | SAMSUNG ä¸‰æ˜Ÿ | Very popular
Basic Library | C1546 | 100PF (101) Â±5% 50V C0G | 402 | Capacitor_chip capacitor | Provided by Jiali Chuang | 105197 | Click to view | 0402CG101J500NT | FH é£Žå Ž | Very popular
Basic Library | C1603 | 220PF (221) Â±10% 50V X7R | 603 | Capacitor_chip capacitor | Provided by Jiali Chuang | 76220 | Click to view | CL10B221KB8NNNC | SAMSUNG ä¸‰æ˜Ÿ | Very popular
Basic Library | C1604 | 2.2NF (222) Â±10% 50V X7R | 603 | Capacitor_chip capacitor | Provided by Jiali Chuang | 114993 | Click to view | 0603B222K500NT | FH é£Žå Ž | Very popular
Basic Library | C53987 | 4.7NF (472) Â±10% 50V X7R | 603 | Capacitor_chip capacitor | Provided by Jiali Chuang | 109918 | Click to view | 0603B472K500NT | FH é£Žå Ž | Very popular
Basic Library | C21122 | 22NF (223) Â±10% 50V X7R | 603 | Capacitor_chip capacitor | Provided by Jiali Chuang | 206074 | Click to view | CL10B223KB8NNNC | SAMSUNG ä¸‰æ˜Ÿ | Very popular
Basic Library | C14663 | 100NF (104) Â±10% 50V X7R | 603 | Capacitor_chip capacitor | Provided by Jiali Chuang | 5420907 | Click to view | CC0603KRX7R9BB104 | YAGEO å›½å·¨ | Very popular
Basic Library | C21120 | 220NF (224) Â±10% 25V X7R | 603 | Capacitor_chip capacitor | Provided by Jiali Chuang | 359020 | Click to view | CL10B224KA8NNNC | SAMSUNG ä¸‰æ˜Ÿ | Very popular
Basic Library | C15525 | 10UF (106) Â±20% 6.3V X5R | 402 | Capacitor_chip capacitor | Provided by Jiali Chuang | 67461 | Click to view | CL05A106MQ5NUNC | SAMSUNG ä¸‰æ˜Ÿ | Very popular
Basic Library | C17415 | 10Î© (10R0) Â±1% | 805 | Resistor_chip resistor | Provided by Jiali Chuang | 513978 | Click to view | 0805W8F100JT5E | UNIOHMå °æ¹¾åŽšå£° | Very popular
Basic Library | C17903 | 10Î© (10R0) Â±1% | 1206 | Resistor_chip resistor | Provided by Jiali Chuang | 280345 | Click to view | 1206W4F100JT5E | UNIOHMå °æ¹¾åŽšå£° | Very popular
Basic Library | C16133 | 100UF (107) Â±10% 6.3V | CASE-B_3528 | Tantalum Capacitor | Provided by Jiali Chuang | 106439 | Click to view | TAJB107K006RNJ | AVX | Very popular
Basic Library | C17408 | 100Î© (1000) Â±1% | 805 | Resistor_chip resistor | Provided by Jiali Chuang | 175713 | Click to view | 0805W8F1000T5E | UNIOHMå °æ¹¾åŽšå£° | Very popular
Basic Library | C1015 | 100Î© Â±25% 100MHZ | 805 | Ferrite Bead | Provided by Jiali Chuang | 106052 | Click to view | GZ2012D101TF | SUNLORD é¡ºç»œ | Very popular
Basic Library | C25804 | 10KÎ© (1002) Â±1% | 603 | Resistor_chip resistor | Provided by Jiali Chuang | 8942399 | Click to view | 0603WAF1002T5E | UNIOHMå °æ¹¾åŽšå£° | Very popular
Basic Library | C17902 | 10KÎ© (1002) Â±1% | 1206 | Resistor_chip resistor | Provided by Jiali Chuang | 217362 | Click to view | 1206W4F1002T5E | UNIOHMå °æ¹¾åŽšå£° | Very popular
Basic Library | C17407 | 100KÎ© (1003) Â±1% | 805 | Resistor_chip resistor | Provided by Jiali Chuang | 691501 | Click to view | 0805W8F1003T5E | UNIOHMå °æ¹¾åŽšå£° | Very popular
Basic Library | C22787 | 120Î© (1200) Â±1% | 603 | Resistor_chip resistor | Provided by Jiali Chuang | 28285 | Click to view | 0603WAF1200T5E | UNIOHMå °æ¹¾åŽšå£° | Very popular
Basic Library | C22807 | 150KÎ© (1503) Â±1% | 603 | Resistor_chip resistor | Provided by Jiali Chuang | 24575 | Click to view | 0603WAF1503T5E | UNIOHMå °æ¹¾åŽšå£° | Very popular
Basic Library | C23630 | 2.2UF (225) Â±10% 16V X5R | 603 | Capacitor_chip capacitor | Provided by Jiali Chuang | 283926 | Click to view | CL10A225KO8NNNC | SAMSUNG ä¸‰æ˜Ÿ | Very popular
Basic Library | C17604 | 2KÎ© (2001) Â±1% | 805 | Resistor_chip resistor | Provided by Jiali Chuang | 1520376 | Click to view | 0805W8F2001T5E | UNIOHMå °æ¹¾åŽšå£° | Very popular
Basic Library | C4109 | 2KÎ© (2001) Â±1% | 402 | Resistor_chip resistor | Provided by Jiali Chuang | 160142 | Click to view | 0402WGF2001TCE | UNIOHMå °æ¹¾åŽšå£° | Very popular
Basic Library | C4328 | 20KÎ© (2002) Â±1% | 805 | Resistor_chip resistor | Provided by Jiali Chuang | 299010 | Click to view | 0805W8F2002T5E | UNIOHMå °æ¹¾åŽšå£° | Very popular
Basic Library | C59461 | 22UF (226) Â±20% 6.3V X5R | 603 | Capacitor_chip capacitor | Provided by Jiali Chuang | 145212 | Click to view | CL10A226MQ8NRNC | SAMSUNG ä¸‰æ˜Ÿ | Very popular
Basic Library | C25092 | 22Î© (22R0) Â±1% | 402 | Resistor_chip resistor | Provided by Jiali Chuang | 83190 | Click to view | 0402WGF220JTCE | UNIOHMå °æ¹¾åŽšå£° | Very popular
Basic Library | C22962 | 220Î© (2200) Â±1% | 603 | Resistor_chip resistor | Provided by Jiali Chuang | 60305 | Click to view | 0603WAF2200T5E | UNIOHMå °æ¹¾åŽšå£° | Very popular
Basic Library | C17520 | 2.2KÎ© (2201) Â±1% | 805 | Resistor_chip resistor | Provided by Jiali Chuang | 215191 | Click to view | 0805W8F2201T5E | UNIOHMå °æ¹¾åŽšå£° | Very popular
Basic Library | C84635 | SS34 | SMA,DO-214AC | Diode_Schottky diode | Provided by Jiali Chuang | 13282 | Click to view | SS34 | è¿ªä¸€ | Very popular | SMT Phase IV - Extended Library
Basic Library | C22452 | SS54 | SMA,DO-214AC | Diode_Schottky diode | Provided by Jiali Chuang | 147255 | Click to view | SS54 | LC ç«‹åˆ› | Very popular | SMT Phase IV - Extended Library
Basic Library | C8734 | STM32F103C8T6 | LQFP-48_7X7X05P | Microcontroller (MCU) | Provided by Jiali Chuang | 25189 | Click to view | STM32F103C8T6 | ST æ„ æ³•å Šå¯¼ä½“ | Very popular
Basic Library | C95872 | 1N4007 M7 | SMA,DO-214AC | Diode_General Diode | Provided by Jiali Chuang | 746045 | Click to view | M7 | MDD | Very popular | SMT Phase IV - Extended Library
Basic Library | C6649 | EL357N(B)(TA)-G | SOP-4_P2.54_C6649 | Patch Optocoupler | Provided by Jiali Chuang | 206908 | Click to view | EL357N(B)(TA)-G | EVERLIGHT å °æ¹¾äº¿å…‰ | Very popular
Basic Library | C72043 | Green light | LED_0603 | Diode_LED | Provided by Jiali Chuang | 245510 | Click to view | 19-217/GHC-YR1S2/3T | EVERLIGHT å °æ¹¾äº¿å…‰ | Very popular | LED,LED,LED
Basic Library | C22978 | 3.3KÎ© (3301) Â±1% | 603 | Resistor_chip resistor | Provided by Jiali Chuang | 371674 | Click to view | 0603WAF3301T5E | UNIOHMå °æ¹¾åŽšå£° | Very popular
Basic Library | C15127 | AO3401A Pé “æ²Ÿ X13A15 SOT-23 | SOT-23-3L | MOS_FET | Provided by Jiali Chuang | 70526 | Click to view | AO3401A | AOS | Very popular
Basic Library | C9808 | LL4148 | LL-34 | Diode_switching diode | Provided by Jiali Chuang | 1169372 | Click to view | LL4148 | å…ˆç§‘ST | Very popular | LL4148 LL-34 1206
Basic Library | C17710 | 470Î© (4700) Â±1% | 805 | Resistor_chip resistor | Provided by Jiali Chuang | 297679 | Click to view | 0805W8F4700T5E | UNIOHMå °æ¹¾åŽšå£° | Very popular
Basic Library | C23193 | 510Î© (5100) Â±1% | 603 | Resistor_chip resistor | Provided by Jiali Chuang | 319471 | Click to view | 0603WAF5100T5E | UNIOHMå °æ¹¾åŽšå£° | Very popular
Basic Library | C27834 | 5.1KÎ© (5101) Â±1% | 805 | Resistor_chip resistor | Provided by Jiali Chuang | 754080 | Click to view | 0805 F5101T5E | UNIOHMå °æ¹¾åŽšå£° | Very popular
Basic Library | C8542 | SS8550 | SOT-23 | Transistor | Provided by Jiali Chuang | 483706 | Click to view | SS8550 Y2 200-350 | CJæ±Ÿè‹ é•¿ç”µ | Very popular | SS8550 Y2
Basic Library | C2500 | BAV99 A7W | SOT-23 | Diode_switching diode | Provided by Jiali Chuang | 39893 | Click to view | BAV99 | NXP æ ©æ™ºæµ¦ | Very popular
Basic Library | C2146 | S8050 (200-350) | SOT-23 | Transistor | Provided by Jiali Chuang | 252159 | Click to view | S8050 | CJæ±Ÿè‹ é•¿ç”µ | Very popular
Basic Library | C72041 | Blue light | LED_0603 | Diode_LED | Provided by Jiali Chuang | 179462 | Click to view | 19-217/BHC-ZL1M2RY/3T | EVERLIGHT å °æ¹¾äº¿å…‰ | Very popular | LED,LED,LED
Basic Library | C17888 | 0Î© (0R0) Â±1% | 1206 | Resistor_chip resistor | Provided by Jiali Chuang | 120773 | Click to view | 1206W4F0000T5E | UNIOHMå °æ¹¾åŽšå£° | Very popular
Basic Library | C38523 | 12PF (120) Â±5% 50V C0G | 603 | Capacitor_chip capacitor | Provided by Jiali Chuang | 87512 | Click to view | CL10C120JB8NNNC | SAMSUNG ä¸‰æ˜Ÿ | Very popular
Basic Library | C1647 | 18PF (180) Â±5% 50V C0G | 603 | Capacitor_chip capacitor | Provided by Jiali Chuang | 53634 | Click to view | CL10C180JB8NNNC | SAMSUNG ä¸‰æ˜Ÿ | Very popular
Basic Library | C1555 | 22PF (220) Â±5% 50V C0G | 402 | Capacitor_chip capacitor | Provided by Jiali Chuang | 95535 | Click to view | 0402CG220J500NT | FH é£Žå Ž | Very popular
Basic Library | C46653 | 1NF (102) Â±10% 50V X7R | 805 | Capacitor_chip capacitor | Provided by Jiali Chuang | 166662 | Click to view | CL21B102KBCNNNC | SAMSUNG ä¸‰æ˜Ÿ | Very popular
Basic Library | C1523 | 1NF (102) Â±10% 50V X7R | 402 | Capacitor_chip capacitor | Provided by Jiali Chuang | 93705 | Click to view | 0402B102K500NT | FH é£Žå Ž | Very popular
Basic Library | C57112 | 10NF (103) Â±10% 50V X7R | 603 | Capacitor_chip capacitor | Provided by Jiali Chuang | 1407957 | Click to view | 0603B103K500NT | FH é£Žå Ž | Very popular
Basic Library | C24497 | 100NF (104) Â±10% 50V X7R | 1206 | Capacitor_chip capacitor | Provided by Jiali Chuang | 315603 | Click to view | CL31B104KBCNNNC | SAMSUNG ä¸‰æ˜Ÿ | Very popular
Basic Library | C49678 | 100NF(104) Â±10% 50V X7R | 805 | Capacitor_chip capacitor | Provided by Jiali Chuang | 2543263 | Click to view | CC0805KRX7R9BB104 | YAGEO å›½å·¨ | Very popular
Basic Library | C52923 | 1UF (105) Â±10% 25V X5R | 402 | Capacitor_chip capacitor | Provided by Jiali Chuang | 553551 | Click to view | CL05A105KA5NQNC | SAMSUNG ä¸‰æ˜Ÿ | Very popular
Basic Library | C19702 | 10UF (106) Â±10% 10V X5R | 603 | Capacitor_chip capacitor | Provided by Jiali Chuang | 1524121 | Click to view | CL10A106KP8NNNC | SAMSUNG ä¸‰æ˜Ÿ | Very popular
Basic Library | C13585 | 10UF (106) Â±10% 50V X5R | 1206 | Capacitor_chip capacitor | Provided by Jiali Chuang | 532677 | Click to view | CL31A106KBHNNNE | SAMSUNG ä¸‰æ˜Ÿ | Very popular
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

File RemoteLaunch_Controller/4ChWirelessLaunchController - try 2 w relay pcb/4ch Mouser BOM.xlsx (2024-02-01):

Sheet: Sheet1 (2)
Mouser
Relay board (only in remote)
Item | Designnator | quantity | Desc | Mouser | Manf | Price | notes
1 |  | 2 | 2-pos terminal block | 490-TB007-508-02BE | TB007-508-02BE | 0.73 | power, LED
2 |  | 4 | 4-pos terminal block | 490-TB007-508-04BE | TB007-508-04BE | 1.18 | pad, continuity push button
3 |  | 1 | 8-pos terminal block | 490-TB007-508-08BE | TB007-508-08BE | 1.77
 |  | 5 | SPDT relay 12V | 653-G8N-1U-ASDC12 | G8N-1U-AS DC12 | 1.32
 |  | 5 | 1K 1W resistor | 603-CFR1WSJT-52-1K |  | 0.15
 |  | 1 | pcb |  |  | 10.00
 |  | 4 | 6-32 standoff |  |  | 0.46 | Such as mcmaster-carr 93505A442
 |  |  |  |  |  |  |  | 15.15
launch control and remote board (so qty x 2)
 | IC1 | 1 | Adafruit LoRo Feather | 485-3178 |  | 34.95
 |  | 2 | 2-pos terminal block | 490-TB007-508-02BE | TB007-508-02BE | 0.73 | power, LED
 |  | 2 | 8-pos terminal block | 490-TB007-508-08BE | TB007-508-08BE | 1.77
 |  | 2 | 2-pos terminal block | 571-282834-2 |  | 1.72
 |  | 2 | 3-pos terminal block | 651-1985823 |  |  | optional
 |  | 2 | 3.5 mm audio jack | 490-SJ1-3533NG |  |  | optional
 |  | 1 | header for 3178 | 485-2886 | 2886 | 0.95
 |  | 1 | buzzer | 810-PS1240P02BT |  | 0.58
 | D1 | 1 | green led | 604-APTD2012LCGCK | GREEN | 0.40 | 2MA 1.9V
 | D4 | 1 | red led | 604-APTD2012LSURCK | red | 0.41 | 2m 1.75v
 | D5 | 1 | yellow led | 604-APTD2012LSYCK | yellow | 0.44 | 2ma 1.85v
 | D6 | 1 | orange led | APA2107LSECK/J4-PRV (https://www.mouser.com/ProductDetail/Kingbright/APA2107LSECK-J4-PRV?qs=6oMev5NRZMFINHnQutSYHA%3D%3D) | orange | 0.60 | 2ma 1.8v
 |  | 1 | sma antenna |  |  | 6.25 | https://www.amazon.com/915MHz-LoRa-Gateway-Antenna-Connector/dp/B091PRHPTJ
 |  | 1 | pcb |  |  | 30.00
 |  | 5 | test pont | 534-5010 |  | 0.37
 |  | 4 | 6-32 standoff |  |  | 0.46 | Such as mcmaster-carr 93505A442
 |  | 1 | rectifier protection diode | 70HFR120 |  | 1.40
 |  |  |  |  |  |  |  | 81.03
remote pad obx (relay and remote board)
 |  | 2 | LED |  |  | 0.12 | continuity, power
 |  | 4 | anderson power pole set (two jacks, two terminals, mounting plate) |  |  | 8.00 | battery power, 3 pad channels
 |  | 4 | Anderson mounting plate | 879-1462G1 |  | 6.50
 |  | 2 | SPST toggle |  |  | 3.50 | Power, safety, ? 3rd for heater
 |  | 1 | laser cut panel |  |  | 6.00
 |  |  | Hookup wire |  |  | 6.00
 |  | 1 | sma feedthrough |  |  | 5.00
 |  | 1 | case |  |  | 29.99 | https://www.harborfreight.com/2800-weatherproof-protective-case-medium-orange-58655.html
 |  | 4 | LED holder |  |  | 1.00 | DaierTek 20Pcs 5MM LED Lamp Holder LED Bezel Round Copper Chrome Plated Emitting Diode LED Bezel Holder
 |  |  | Fuse/holder |  |  | 1.00 | https://www.amazon.com/gp/product/B07W4LCP1J/ref=ppx_yo_dt_b_asin_image_o00_s00?ie=UTF8&psc=1
 |  | 3 | push button |  |  | 3.00 | 12mm Metal Boat Horn Momentary Push Button Stainless Steel Starter Switch
 |  |  |  |  |  |  |  | 70.11
 |  |  |  |  |  |  |  | 151.14

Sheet: Sheet1
Mouser
Relay board (only in remote)
Item | Designnator | quantity | Desc | Mouser | Manf | Price | notes
1 |  | 2 | 2-pos terminal block | 490-TB007-508-02BE | TB007-508-02BE | 0.73 | power, LED
2 |  | 4 | 4-pos terminal block | 490-TB007-508-04BE | TB007-508-04BE | 1.18 | pad, continuity push button
3 |  | 1 | 8-pos terminal block | 490-TB007-508-08BE | TB007-508-08BE | 1.77
 |  | 5 | SPDT relay 12V | 653-G8N-1U-ASDC12 | G8N-1U-AS DC12 | 1.32
 |  | 5 | 1K 1W resistor | 603-CFR1WSJT-52-1K |  | 0.15
 |  | 1 | pcb |  |  | 10.00
 |  | 4 | 6-32 standoff |  |  | 0.46 | Such as mcmaster-carr 93505A442
 |  |  |  |  |  |  |  | 15.15
launch control and remote board (so qty x 2)
 | IC1 | 1 | Adafruit LoRo Feather | 485-3178 |  | 34.95
 |  | 2 | 2-pos terminal block | 490-TB007-508-02BE | TB007-508-02BE | 0.73 | power, LED
 |  | 2 | 8-pos terminal block | 490-TB007-508-08BE | TB007-508-08BE | 1.77
 |  | 2 | 2-pos terminal block | 571-282834-2 |  | 1.72
 |  | 2 | 3-pos terminal block | 651-1985823 |  |  | optional
 |  | 2 | 3.5 mm audio jack | 490-SJ1-3533NG |  |  | optional
 |  | 1 | header for 3178 | 485-2886 | 2886 | 0.95
 |  | 1 | buzzer | 810-PS1240P02BT |  | 0.58
 | D1 | 1 | green led | 604-APTD2012LCGCK | GREEN | 0.40 | 2MA 1.9V
 | D4 | 1 | red led | 604-APTD2012LSURCK | red | 0.41 | 2m 1.75v
 | D5 | 1 | yellow led | 604-APTD2012LSYCK | yellow | 0.44 | 2ma 1.85v
 | D6 | 1 | orange led | APA2107LSECK/J4-PRV (https://www.mouser.com/ProductDetail/Kingbright/APA2107LSECK-J4-PRV?qs=6oMev5NRZMFINHnQutSYHA%3D%3D) | orange | 0.60 | 2ma 1.8v
 |  | 1 | sma antenna |  |  | 6.25 | https://www.amazon.com/915MHz-LoRa-Gateway-Antenna-Connector/dp/B091PRHPTJ
 |  | 1 | pcb |  |  | 30.00
 |  | 5 | test pont | 534-5010 |  | 0.37
 |  | 4 | 6-32 standoff |  |  | 0.46 | Such as mcmaster-carr 93505A442
 |  | 1 | rectifier protection diode | 70HFR120 |  | 1.40
 |  |  |  |  |  |  |  | 81.03
remote pad obx (relay and remote board)
 |  | 2 | LED |  |  | 0.12 | continuity, power
 |  | 2 | Buzzer | 665-AI-4228-TWT-R (https://www.mouser.com/ProductDetail/665-AI-4228-TWT-R) |  | 3.88
 |  | 2 | SPST toggle |  |  | 3.50 | Power, safety, ? 3rd for heater
 |  | 3 | anderson power pole set (two jacks, two terminals, mounting plate) |  |  | 2.00 | battery power, 3 pad channels
 |  | 2 | Anderson mounting plate | 879-1462G1 |  | 3.00
 |  | 4 | Heaby duty PB |  |  | 0.50 | continuity
 |  | 1 | XT-60E-60 AMASS plug |  |  | 1.25
 |  | 1 | case |  |  | 29.99 | https://www.harborfreight.com/2800-weatherproof-protective-case-medium-orange-58655.html
 |  | 1 | laser cut panel
 |  |  | Hookup wire
 |  | 1 | sma feedthrough
 |  | 1 | XT-60E-M AMASS make panel pulg |  |  | 1.25 | Adasea 6 Pcs XT60E-M Mountable XT60 Male Plug Connector for RC Models Multicopter
 |  | 2 | LED holder |  |  | 0.50 | DaierTek 20Pcs 5MM LED Lamp Holder LED Bezel Round Copper Chrome Plated Emitting Diode LED Bezel Holder
 |  |  | Fuse/holder |  |  |  | DaierTek Inline Fuse Holder 12 AWG Waterproof ATC/ATO Blade Fuse Holder with 20 Amp 30 Amp 40 Amp Inline Fuse Heavy Duty in Line Fuse Holder 12V for Marine Automotive Vehicle
 |  |  |  |  |  |  |  | #REF!
launch control box
 |  | 1 | LED |  |  | 0.12 | power
 |  | 2 | SPST toggle |  |  | 3.50 | Power, safety, ? 3rd for heater
 |  | 1 | anderson power pole set (two jacks, two terminals, mounting plate) |  |  | 2.00 | battery power
 |  | 1 | Heaby duty PB |  |  | 5.75 | APIELE 16mm Momentary Push Button Switch High Round Cap Waterproof Stainless Steel High Flush Screw Terminals 250V AC 5A 12V 36V DC 2A 1NO SPST
 |  | 1 | XT-60E-60 AMASS plug |  |  | 1.25
 |  | 1 | case |  |  | 29.99 | https://www.harborfreight.com/2800-weatherproof-protective-case-medium-orange-58655.html
 |  | 5 | Momentary SPST toggle |  |  | 3.75 | Twidec/3Pcs Heavy Duty Rocker Momentary Toggle Switch 16A 250V AC SPDT 3 Position 3 Pin (ON)-Off-(ON) Switch with Metal Bat Waterproof Boot Cap Cover Ten-123-B123
 |  | 1 | sma feedthrough
 |  | 1 | Led holder |  |  | 0.50
 |  | 1 | Fuse/holder |  |  | 3.00 | DaierTek Inline Fuse Holder 12 AWG Waterproof ATC/ATO Blade Fuse Holder with 20 Amp 30 Amp 40 Amp Inline Fuse Heavy Duty in Line Fuse Holder 12V for Marine Automotive Vehicle

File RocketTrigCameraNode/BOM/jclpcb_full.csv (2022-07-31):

Comment | Designator | Footprint | LCSC
Buzzer | BZ1 | Buzzer_Beeper:Buzzer_Murata_PKMCS0909E4000-R1 | C255322
0.01 μF | C1,C2,C5,C6,C7,C8,C9 | Capacitor_SMD:C_0402_1005Metric | C1525
1uf | C3 | Capacitor_SMD:CP_Elec_4x5.4 | C87863
25uf | C4 | Capacitor_SMD:C_Elec_4x5.4 | C2895283
100n | C51 | Capacitor_SMD:C_0402_1005Metric | C1525
LED Arm | D1 | LED_SMD:LED_0603_1608Metric | C389521
LED Trig | D2 | LED_SMD:LED_0603_1608Metric | C264544
PWR | D3 | LED_SMD:LED_0603_1608Metric | C264544
B330A-13-F | D4 | Diode_SMD:D_SMA | C110485
LED Trig | D5 | LED_THT:LED_D3.0mm
BLUE | D51 | LED_SMD:LED_0603_1608Metric | C72041
LED Focus | D6 | LED_THT:LED_D3.0mm
TestPoint | GND1 | TestPoint:TestPoint_Keystone_5000-5004_Miniature
 | H1,H2,H3,H4 | MountingHole:MountingHole_3.7mm_Pad
3178 | IC1 | 3178
 | J1 | Connector_PinHeader_2.54mm:PinHeader_1x05_P2.54mm_Vertical
qwiic | J10 | Connector_JST:JST_SH_BM04B-SRSS-TB_1x04-1MP_P1.00mm_Vertical | C160404
Micro_SD_Card | J11 | Connector_Card:microSD_HC_Hirose_DM3AT-SF-PEJM5 | C114218
XLR5 Male | J2 | SamacSys_Parts:Jack_XLR_Neutrik_NC5MBH_Horizontal
 | J3 | Connector_PinHeader_1.27mm:PinHeader_1x06_P1.27mm_Vertical
 | J4 | Connector_PinHeader_1.27mm:PinHeader_1x09_P1.27mm_Vertical
Aux out | J5 | TerminalBlock_TE-Connectivity:TerminalBlock_TE_282834-2_1x02_P2.54mm_Horizontal
 | J6 | Connector_AMASS:AMASS_XT30U-F_1x02_P5.0mm_Vertical
Trig in | J7 | TerminalBlock_TE-Connectivity:TerminalBlock_TE_282834-2_1x02_P2.54mm_Horizontal
Camera 3.5mm | J8 | Connector_Audio:Jack_3.5mm_CUI_SJ1-3533NG_Horizontal_CircularHoles
Camera 2.5mm | J9 | CameraTriggerPCB:CUI_SJ1-2503A
MMBT3904 | Q1,Q3,Q4 | Package_TO_SOT_SMD:SOT-23 | C8512
2SC1815 | Q2 | Package_TO_SOT_SMD:SOT-23 | C181171
1K | R1,R2,R3,R5,R6,R7,R9 | Resistor_SMD:R_0603_1608Metric | C21190
50 | R8,R10 | Resistor_SMD:R_0603_1608Metric
0 | R11,R12 | Resistor_SMD:R_0603_1608Metric | C21189
0 | R13 | Resistor_SMD:R_1206_3216Metric_Pad1.42x1.75mm_HandSolder | C269749
5K | R4 | Resistor_SMD:R_0402_1005Metric | C25744
1k5 | R51 | Resistor_SMD:R_0603_1608Metric | C22843
 | SW1 | Button_Switch_THT:SW_Slide_1P2T_CK_OS102011MS2Q
AS11CB | SW2 | CameraTriggerPCB:AS11CB
SW_trig | SW3 | Button_Switch_THT:KSA_Tactile_SPST
SW_Poll | SW4 | Button_Switch_THT:KSA_Tactile_SPST
SW_Arm | SW5 | Button_Switch_THT:KSA_Tactile_SPST
Sensor | TP1 | TestPoint:TestPoint_Keystone_5000-5004_Miniature
+5V | TP1+1 | TestPoint:TestPoint_Keystone_5010-5014_Multipurpose
Gnd | TP2 | TestPoint:TestPoint_Keystone_5000-5004_Miniature
Fire | TP4Fire1 | TestPoint:TestPoint_Keystone_5010-5014_Multipurpose
LM7805_TO220 | U1 | Package_TO_SOT_SMD:TO-252-2 | C310413
ILD74 | U2,U3 | Package_DIP:DIP-8_W7.62mm
CD4050BDR | U4 | Package_SO:SOP-16_4.4x10.4mm_P1.27mm | C352821
RN4871 | U5 | RF_Module:Microchip_RN4871

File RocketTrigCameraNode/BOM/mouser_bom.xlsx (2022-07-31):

Comment | Designator | Footprint | Mouser
25uf | C4 | Capacitor_SMD:C_Elec_4x5.4
TestPoint | GND1 | TestPoint:TestPoint_Keystone_5000-5004_Miniature
3178 | IC1 | 3178 | 485-3176
 | J1 | Connector_PinHeader_2.54mm:PinHeader_1x05_P2.54mm_Vertical
XLR5 Male | J2 | SamacSys_Parts:Jack_XLR_Neutrik_NC5MBH_Horizontal | 568-NC5MBH
Aux out | J3 | TerminalBlock_TE-Connectivity:TerminalBlock_TE_282834-2_1x02_P2.54mm_Horizontal | 571-282834-2
 | J4 | Connector_AMASS:AMASS_XT30U-F_1x02_P5.0mm_Vertical
 | J5 | 19-237_R6GHBHC-A01_2T:HDRV4W64P0X254_1X4_1016X635X1067P
Conn_01x04_Male | J7 | 19-237_R6GHBHC-A01_2T:HDRV4W64P0X254_1X4_1016X635X1067P
Serial | J8 | TerminalBlock_TE-Connectivity:TerminalBlock_TE_282834-4_1x04_P2.54mm_Horizontal | 571-282834-4
Analog in | J9 | TerminalBlock_TE-Connectivity:TerminalBlock_TE_282834-2_1x02_P2.54mm_Horizontal | 571-282834-2
1K | RV1 | Potentiometer_THT:Potentiometer_Alps_RK09K_Single_Vertical | 688-RK09K1130AV7 (https://www.mouser.com/ProductDetail/688-RK09K1130AV7)
 | SW1 | Button_Switch_THT:SW_Slide_1P2T_CK_OS102011MS2Q | 611-OS102011MS2QN1
AS11CB | SW2 | CameraTriggerPCB:AS11CB | 633-AS11CP (https://www.mouser.com/ProductDetail/633-AS11CP)
SW_Poll | SW3 | Button_Switch_THT:KSA_Tactile_SPST | 611-KSA0A311LFT (https://www.mouser.com/ProductDetail/611-KSA0A311LFT)
SW_Arm | SW4 | Button_Switch_THT:KSA_Tactile_SPST | 611-KSA0A311LFT (https://www.mouser.com/ProductDetail/611-KSA0A311LFT)
Sensor | TP1 | TestPoint:TestPoint_Keystone_5000-5004_Miniature
+5V | TP1+1 | TestPoint:TestPoint_Keystone_5010-5014_Multipurpose
Gnd | TP2 | TestPoint:TestPoint_Keystone_5000-5004_Miniature
 |  | Header | 485-2886
 |  | Antenna | ANT-916-CW-RAH-SMA
 |  | qwiic | 474-PRT-14417
25uf | C4 | Capacitor_SMD:C_Elec_4x5.4
TestPoint | GND1 | TestPoint:TestPoint_Keystone_5000-5004_Miniature
3178 | IC1 | 3178 | 485-3176
 | J1 | Connector_PinHeader_2.54mm:PinHeader_1x05_P2.54mm_Vertical
XLR5 Male | J2 | SamacSys_Parts:Jack_XLR_Neutrik_NC5MBH_Horizontal | 568-NC5MBH
Aux out | J3 | TerminalBlock_TE-Connectivity:TerminalBlock_TE_282834-2_1x02_P2.54mm_Horizontal | 571-282834-2
 | J4 | Connector_AMASS:AMASS_XT30U-F_1x02_P5.0mm_Vertical
 | J5 | 19-237_R6GHBHC-A01_2T:HDRV4W64P0X254_1X4_1016X635X1067P
Conn_01x04_Male | J7 | 19-237_R6GHBHC-A01_2T:HDRV4W64P0X254_1X4_1016X635X1067P
Serial | J8 | TerminalBlock_TE-Connectivity:TerminalBlock_TE_282834-4_1x04_P2.54mm_Horizontal | 571-282834-4
Analog in | J9 | TerminalBlock_TE-Connectivity:TerminalBlock_TE_282834-2_1x02_P2.54mm_Horizontal | 571-282834-2
1K | RV1 | Potentiometer_THT:Potentiometer_Alps_RK09K_Single_Vertical | 688-RK09K1130AV7 (https://www.mouser.com/ProductDetail/688-RK09K1130AV7)
 | SW1 | Button_Switch_THT:SW_Slide_1P2T_CK_OS102011MS2Q | 611-OS102011MS2QN1
AS11CB | SW2 | CameraTriggerPCB:AS11CB | 633-AS11CP (https://www.mouser.com/ProductDetail/633-AS11CP)
SW_Poll | SW3 | Button_Switch_THT:KSA_Tactile_SPST | 611-KSA0A311LFT (https://www.mouser.com/ProductDetail/611-KSA0A311LFT)
SW_Arm | SW4 | Button_Switch_THT:KSA_Tactile_SPST | 611-KSA0A311LFT (https://www.mouser.com/ProductDetail/611-KSA0A311LFT)
Sensor | TP1 | TestPoint:TestPoint_Keystone_5000-5004_Miniature
+5V | TP1+1 | TestPoint:TestPoint_Keystone_5010-5014_Multipurpose
Gnd | TP2 | TestPoint:TestPoint_Keystone_5000-5004_Miniature
 |  | Header | 485-2886
 |  | Antenna | ANT-916-CW-RAH-SMA
 |  | qwiic | 474-PRT-14417

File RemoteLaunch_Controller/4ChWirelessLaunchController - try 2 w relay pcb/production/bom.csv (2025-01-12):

Designator | Footprint | Quantity | Value | LCSC Part #
H1, H2, H3, H4 | MountingHole_5.3mm_M5_DIN965_Pad | 4 | MountingHole
J1 | CUI_TB007-508-02BE | 1 | Pad power and switch
J2 | CUI_TB007-508-06BE | 1 | Control board
J3 | CUI_TB007-508-04BE | 1 | Pad ch 1
J4 | CUI_TB007-508-04BE | 1 | Pad ch 2
J5 | CUI_TB007-508-04BE | 1 | Pad ch 3
J6 | CUI_TB007-508-04BE | 1 | Pad ch 4
J7 | CUI_TB007-508-02BE | 1 | Armed siren
J8 | CUI_TB007-508-02BE | 1 | LED/Buzzer Continuity indicator
J9 | CUI_TB007-508-02BE | 1 | LED power indicator
K1, K3, K4, K5 | RELAY_G8N-1U-DC12 | 4 | G8N-1U-DC12
K2 | RELAY_G8N-1U-DC12 | 1 | Ch 1 relay
R1 | R_Axial_DIN0207_L6.3mm_D2.5mm_P7.62mm_Horizontal | 1 | 1000
R2, R3, R4, R5 | R_Axial_DIN0207_L6.3mm_D2.5mm_P7.62mm_Horizontal | 4 | 1000 ohm
R6 | R_Axial_DIN0207_L6.3mm_D2.5mm_P7.62mm_Horizontal | 1 | R

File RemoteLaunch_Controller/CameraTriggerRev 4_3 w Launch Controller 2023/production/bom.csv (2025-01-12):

Designator | Footprint | Quantity | Value | LCSC Part #
BZ1 | Buzzer_TDK_PS1240P02BT_D12.2mm_H6.5mm | 1 | Buzzer
C1 | CP_Elec_4x5.4 | 1 | 1uf | C87863
C2 | C_Elec_4x5.4 | 1 | 25uf | C2895283
C3, C4 | 0402 | 2 | 0.01 μF | C1525
D1 | 0805 | 1 | D_1
D2 | 0603 | 1 | PWR | C2286
D3 | D_SMA | 1 | B330A-13-F | C110485
D4 | 0805 | 1 | LED Trig
D5 | 0805 | 1 | LED Focus
D6 | 0805 | 1 | D_2
H1, H2, H3, H4, H5 | MountingHole_3.7mm_Pad | 5
IC1 | 3178 | 1 | 3178
J1 | CUI_TB007-508-02BE | 1 | Pwr switch
J10 | AMASS_XT30U-F_1x02_P5.0mm_Vertical | 1 | SW
J11 | CUI_TB007-508-02BE | 1 | pwr
J12, J13 | TerminalBlock_TE_282834-2_1x02_P2.54mm_Horizontal | 2 | Screw_Terminal_01x02
J2 | Jack_3.5mm_CUI_SJ1-3533NG_Horizontal_CircularHoles | 1 | Camera 1 3.5mm
J3 | Jack_3.5mm_CUI_SJ1-3533NG_Horizontal_CircularHoles | 1 | Camera 2 3.5 mm
J4 | TerminalBlock_TE_282834-3_1x03_P2.54mm_Horizontal | 1 | Camera 1 Term
J5 | TerminalBlock_TE_282834-3_1x03_P2.54mm_Horizontal | 1 | Camera 2 Term
J6 | JST_SH_SM04B-SRSS-TB_1x04-1MP_P1.00mm_Horizontal | 1 | qwiic | C160404
J7 | TB00750812BE | 1 | In
J8 | TB00750812BE | 1 | Out
J9 | PinHeader_1x09_P2.54mm_Vertical | 1 | Conn_01x09_Socket
JP1 | SolderJumper-2_P1.3mm_Open_TrianglePad1.0x1.5mm | 1
Q1, Q4 | SOT-23-3 | 2 | 2SC1815 | C181171
Q2, Q3 | SOT-23 | 2 | MMBT3904 | C8512
R1, R13 | 0603 | 2 | 750 | C23241
R10, R9 | 0805 | 2 | 0 | C17477
R11, R12 | 0603 | 2 | 10K | C25804
R14, R15, R2, R3, R4, R5, R7 | 0603 | 7 | 1K | C21190
R6, R8 | 0603 | 2 | 51 | C880145
TP1+1, TP2_5 | TestPoint_Keystone_5010-5014_Multipurpose | 2 | +5V
TP1_GND1 | TestPoint_Keystone_5010-5014_Multipurpose | 1 | GND
TP3_3_3 | TestPoint_Keystone_5010-5014_Multipurpose | 1 | +3.3V
TP4Fire1 | TestPoint_Keystone_5010-5014_Multipurpose | 1 | Fire
TP4_12 | TestPoint_Keystone_5010-5014_Multipurpose | 1 | +12
TP5 | TestPoint_Keystone_5000-5004_Miniature | 1 | Gnd
U1 | SOT-223 | 1 | AMS1117CD-5.0 | C6187
U2 | SOIC-16_4.55x10.3mm_P1.27mm | 1 | TLP291-4 | C60900
U4 | SOIC-28W_7.5x17.9mm_P1.27mm | 1 | MCP23017T-E/SO | C629440
U5 | SOIC127P1030X265-18N | 1 | ULN2803A | C9683

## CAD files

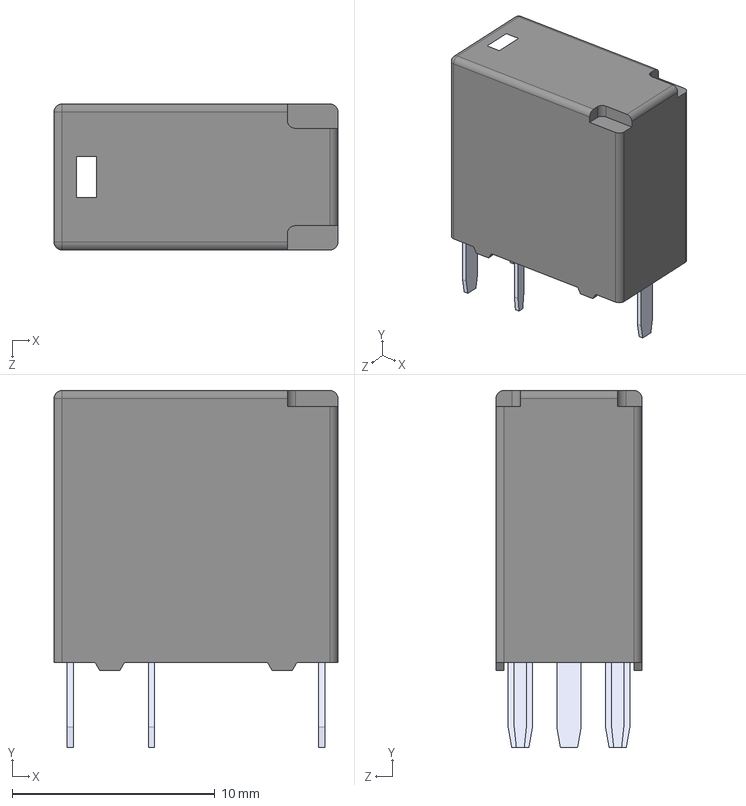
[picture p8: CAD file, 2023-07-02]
RemoteLaunch_Controller/CameraTriggerRev 4_3 w Launch Controller 2023/Footprints/G8N-1U-DC12(1)/G8N-1U-DC12.step
14.0 x 17.6 x 7.20 mm

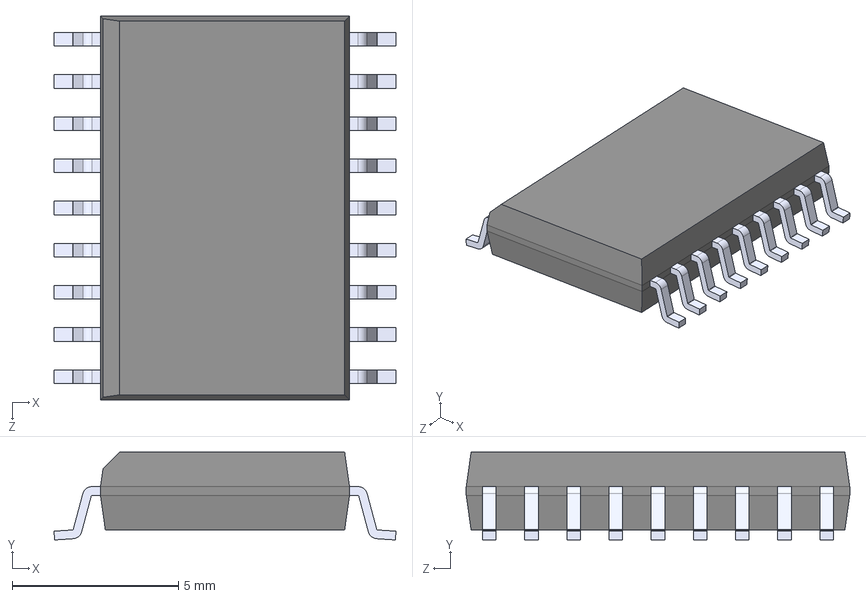
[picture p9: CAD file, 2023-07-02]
RemoteLaunch_Controller/CameraTriggerRev 4_3 w Launch Controller 2023/Footprints/ULN2803ADWR/ULN2803ADWR.step
10.3 x 2.65 x 11.6 mm

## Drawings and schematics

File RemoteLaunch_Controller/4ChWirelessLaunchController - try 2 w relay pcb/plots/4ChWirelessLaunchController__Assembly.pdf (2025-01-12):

# MountingHole H3 MountingHole H4

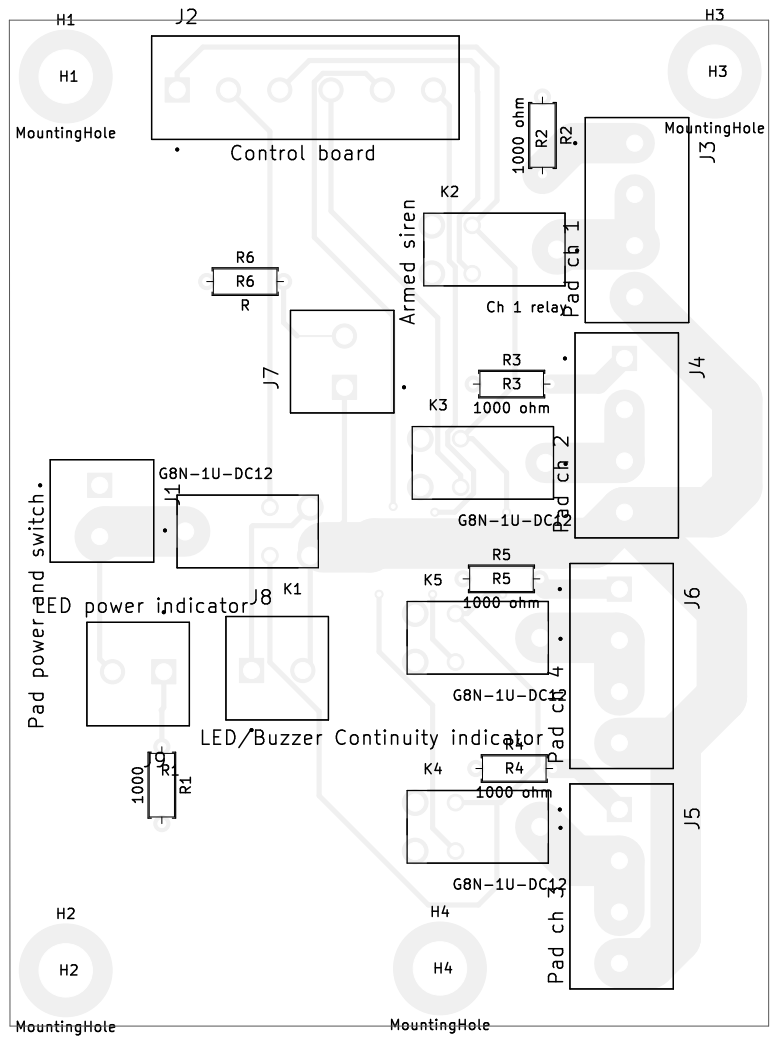
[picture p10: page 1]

R5 LED power indicator MountingHole H1 MountingHole H2

Id: 1/1 Title: File: 4ChWirelessLaunchController.kicad_pcb Sheet: Pad ch 4 R

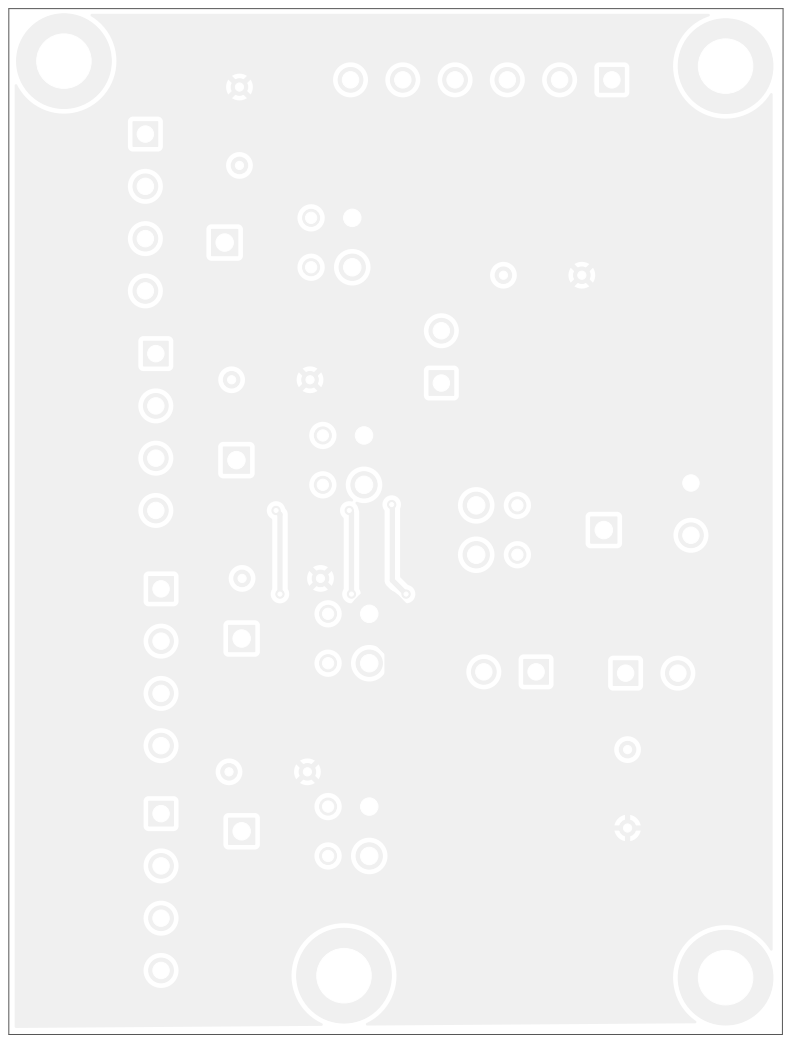
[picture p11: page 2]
D Date: KiCad; E.D.A. kicad; 7.0.5 Size: A4; Rev:

Id: 1/1 Title: File: 4ChWirelessLaunchController.kicad_pcb Sheet:

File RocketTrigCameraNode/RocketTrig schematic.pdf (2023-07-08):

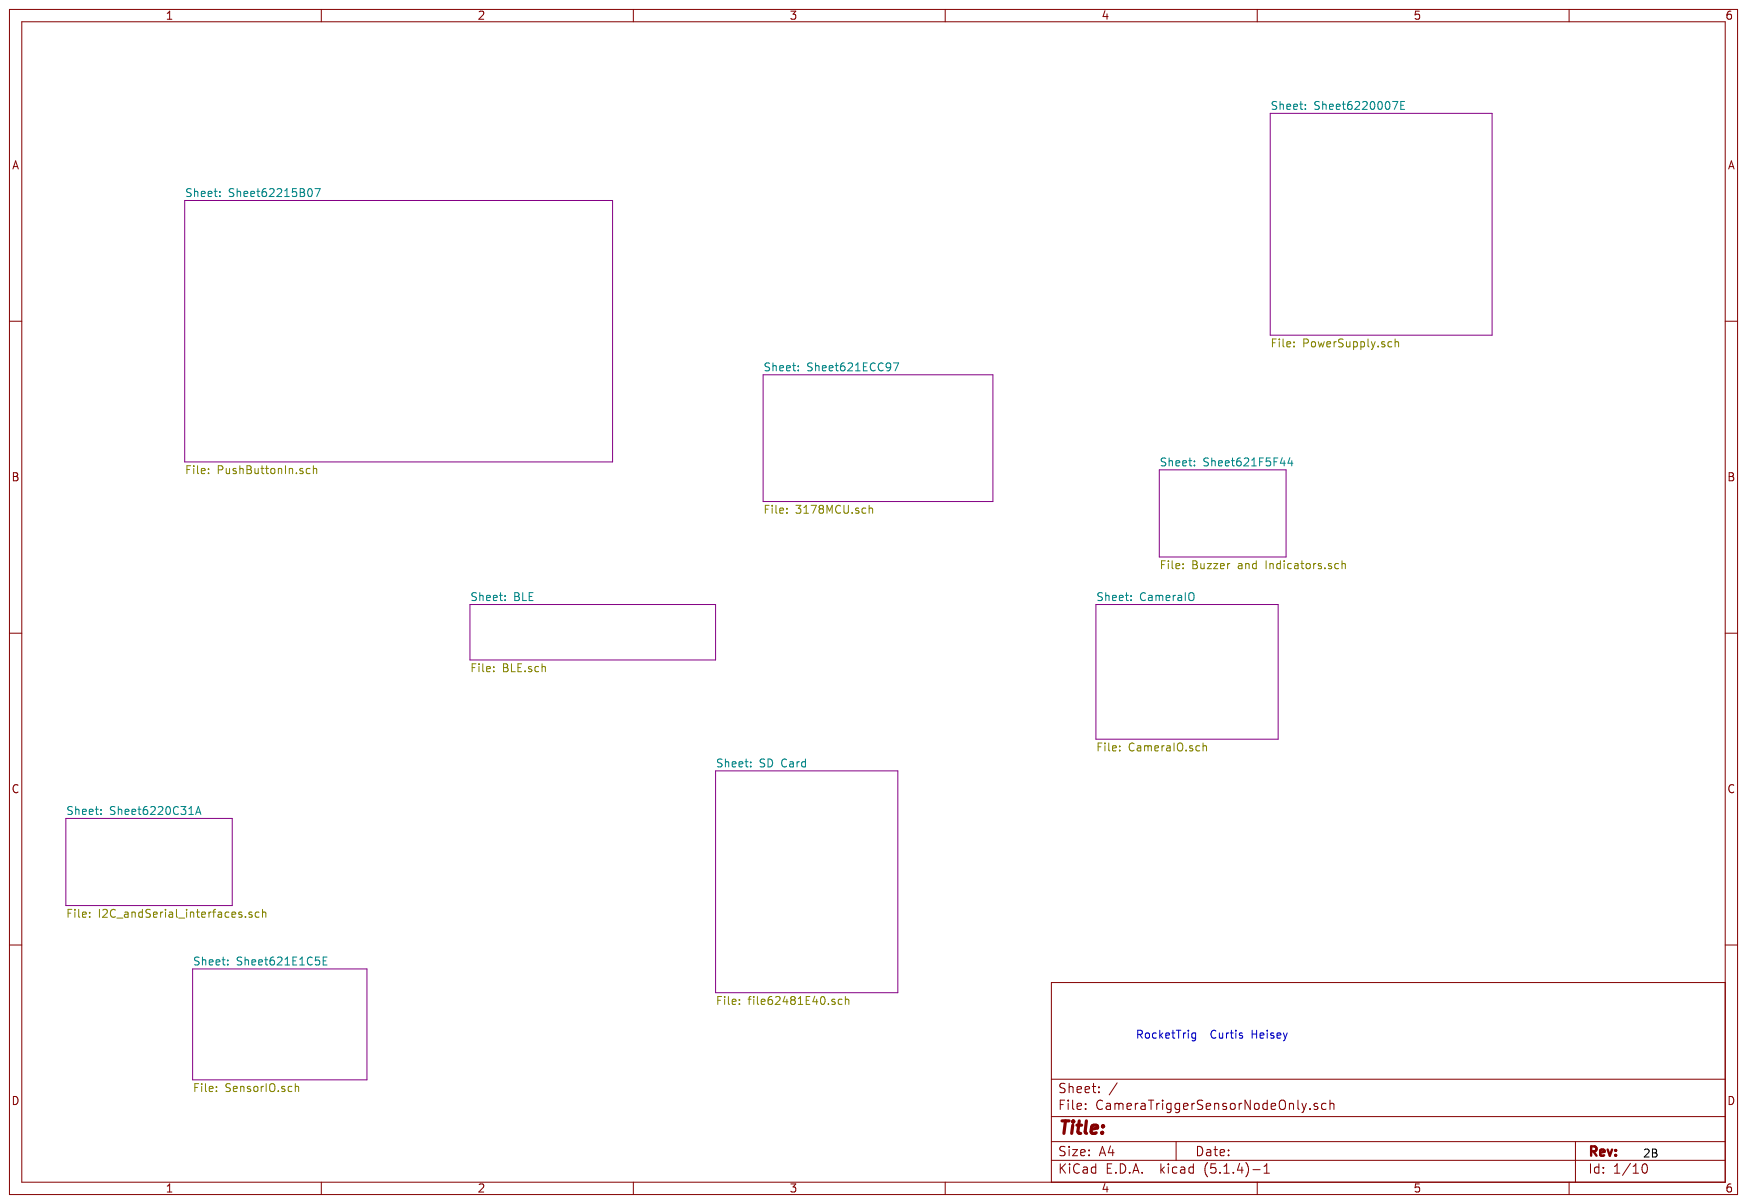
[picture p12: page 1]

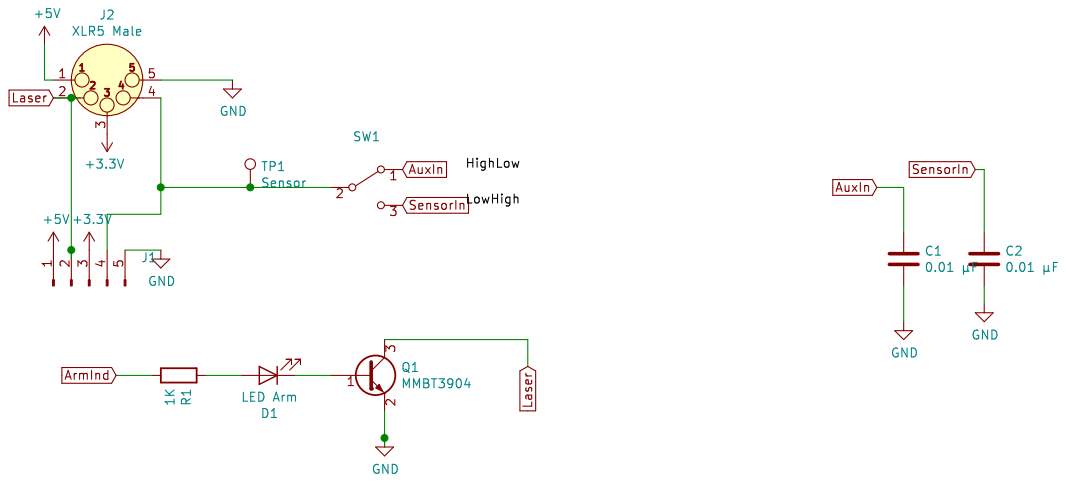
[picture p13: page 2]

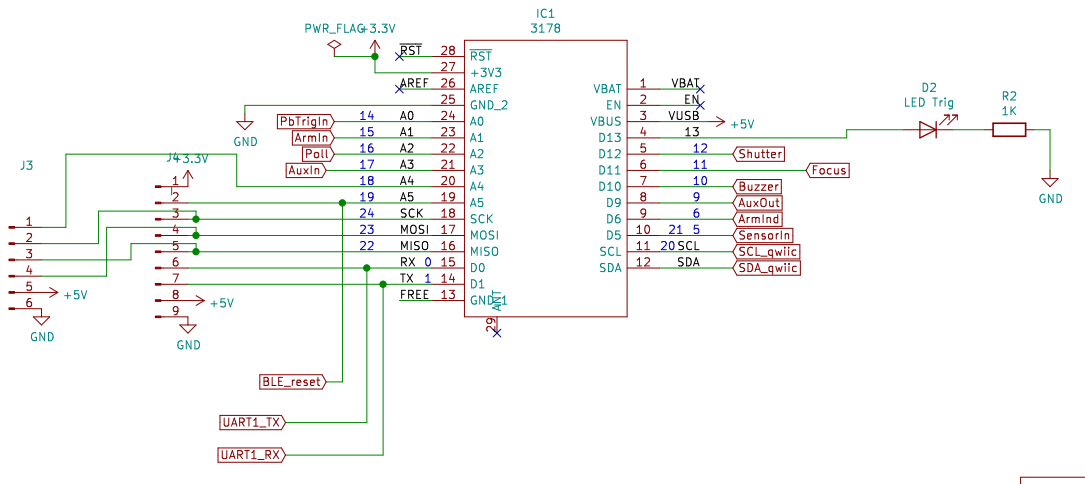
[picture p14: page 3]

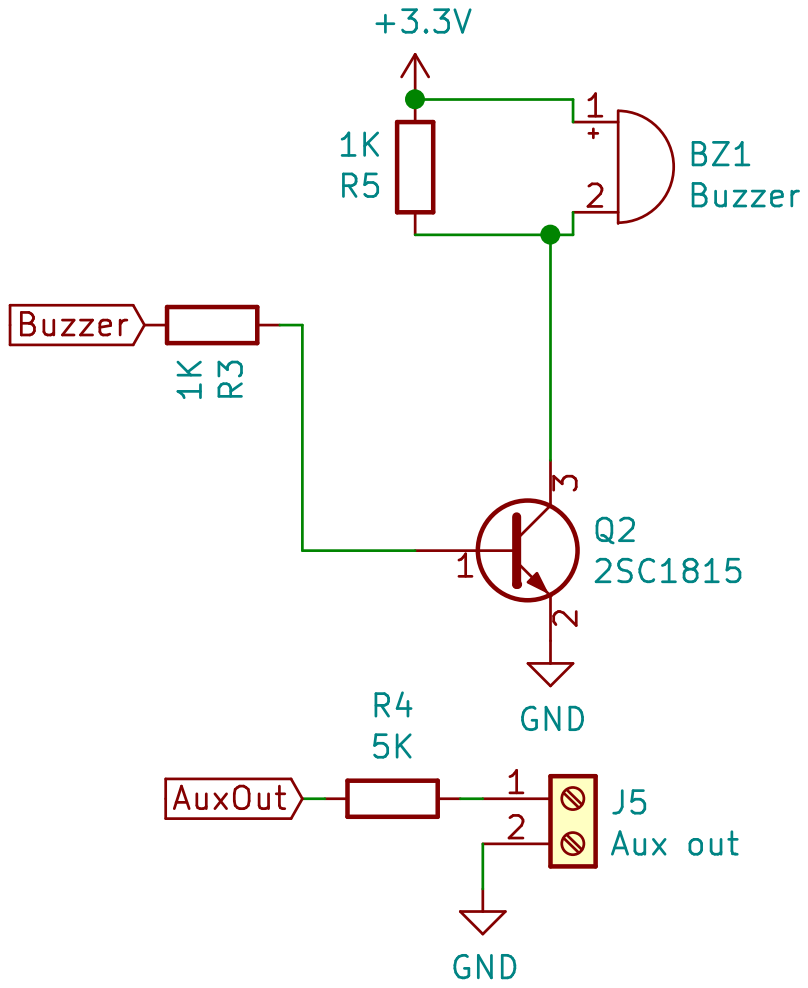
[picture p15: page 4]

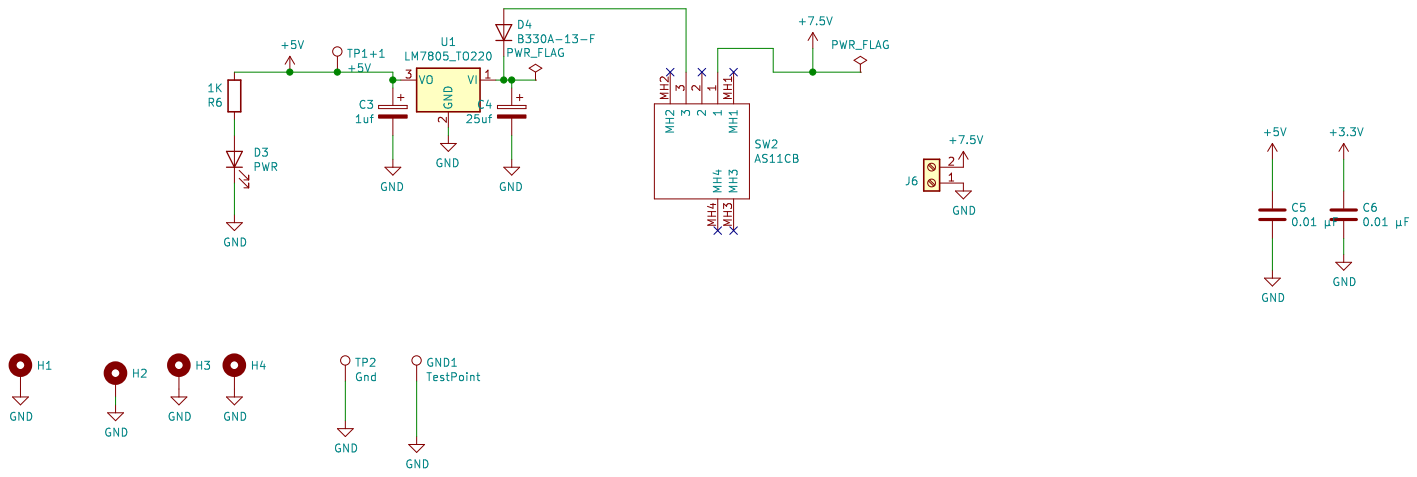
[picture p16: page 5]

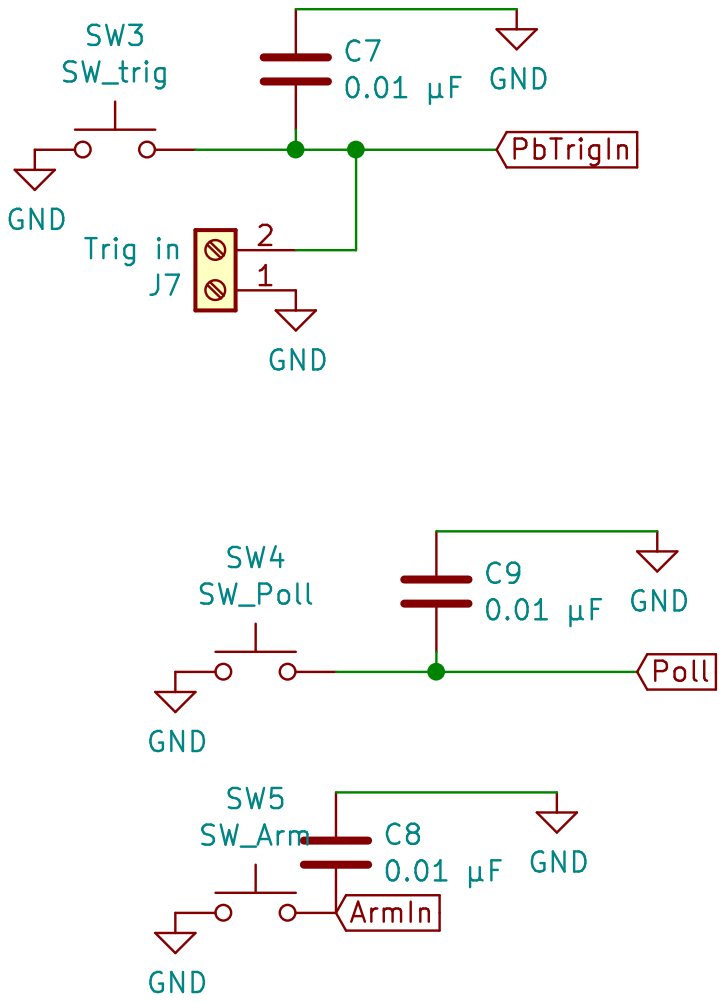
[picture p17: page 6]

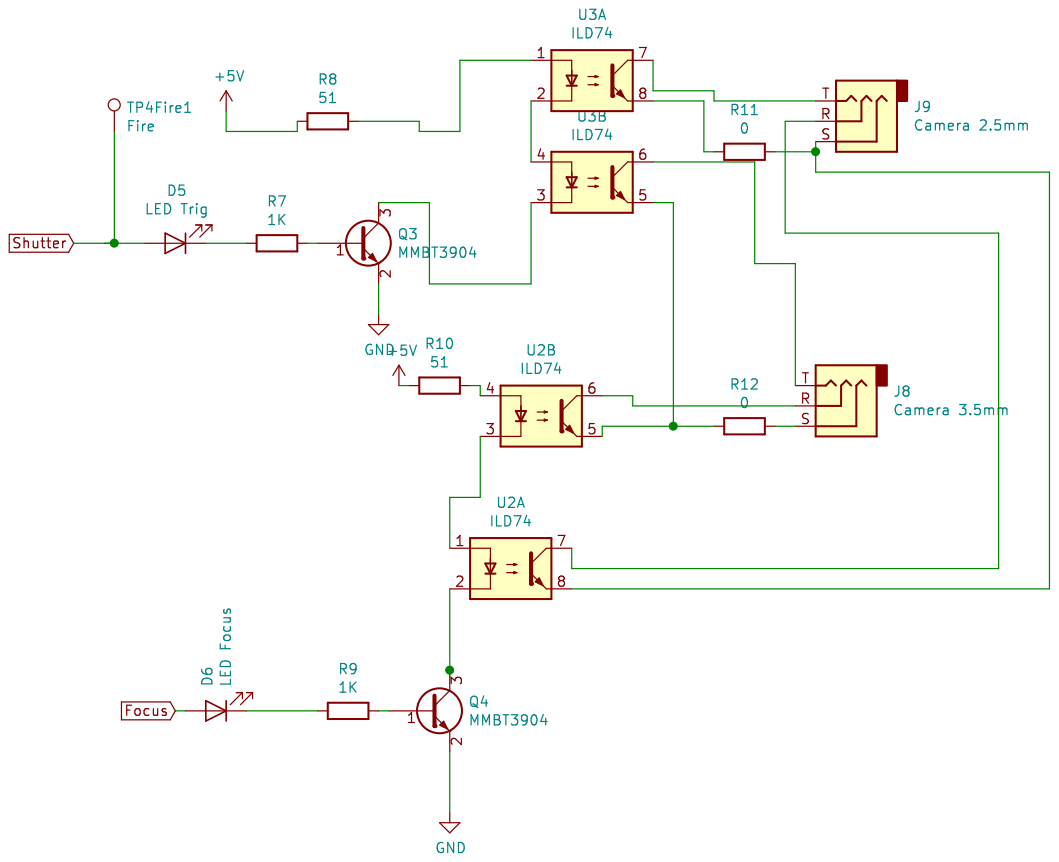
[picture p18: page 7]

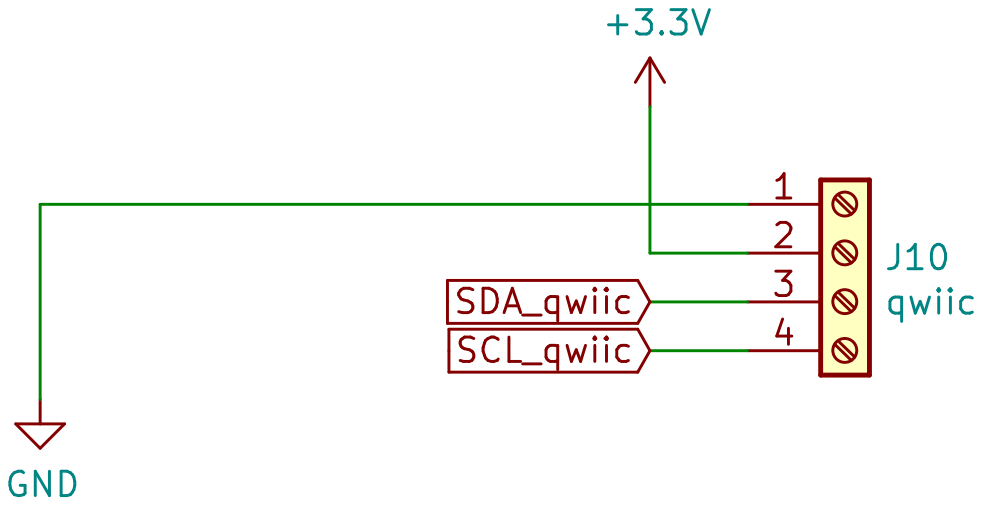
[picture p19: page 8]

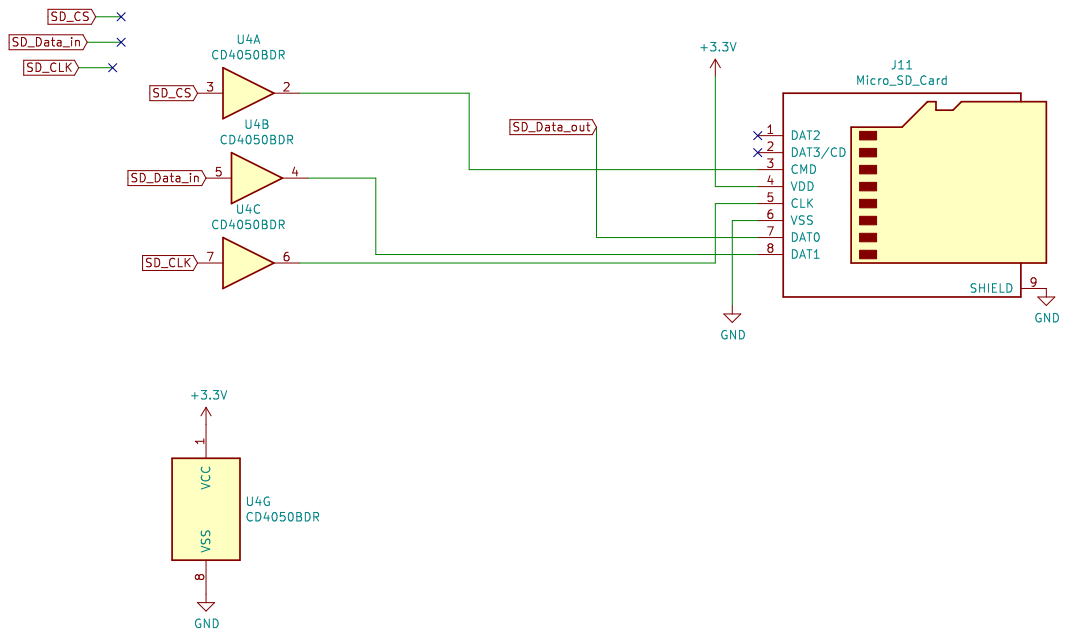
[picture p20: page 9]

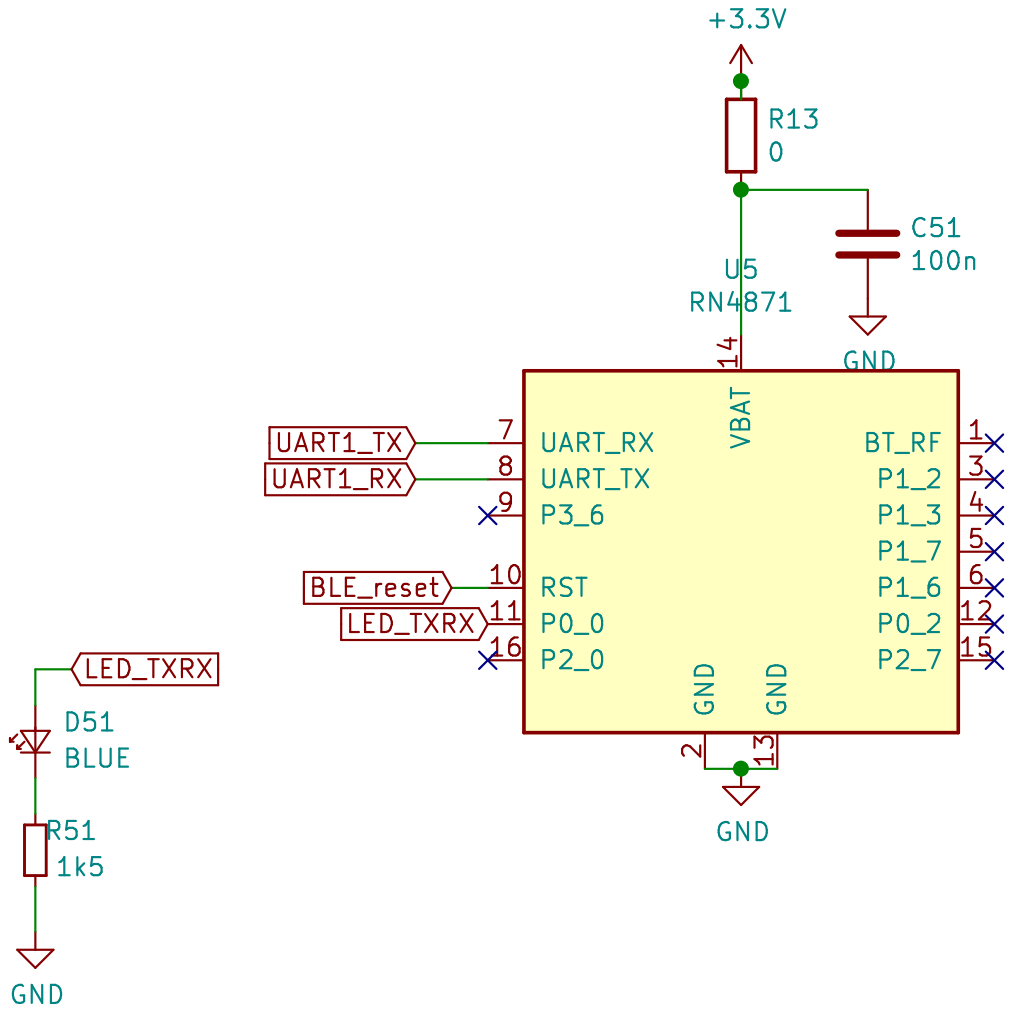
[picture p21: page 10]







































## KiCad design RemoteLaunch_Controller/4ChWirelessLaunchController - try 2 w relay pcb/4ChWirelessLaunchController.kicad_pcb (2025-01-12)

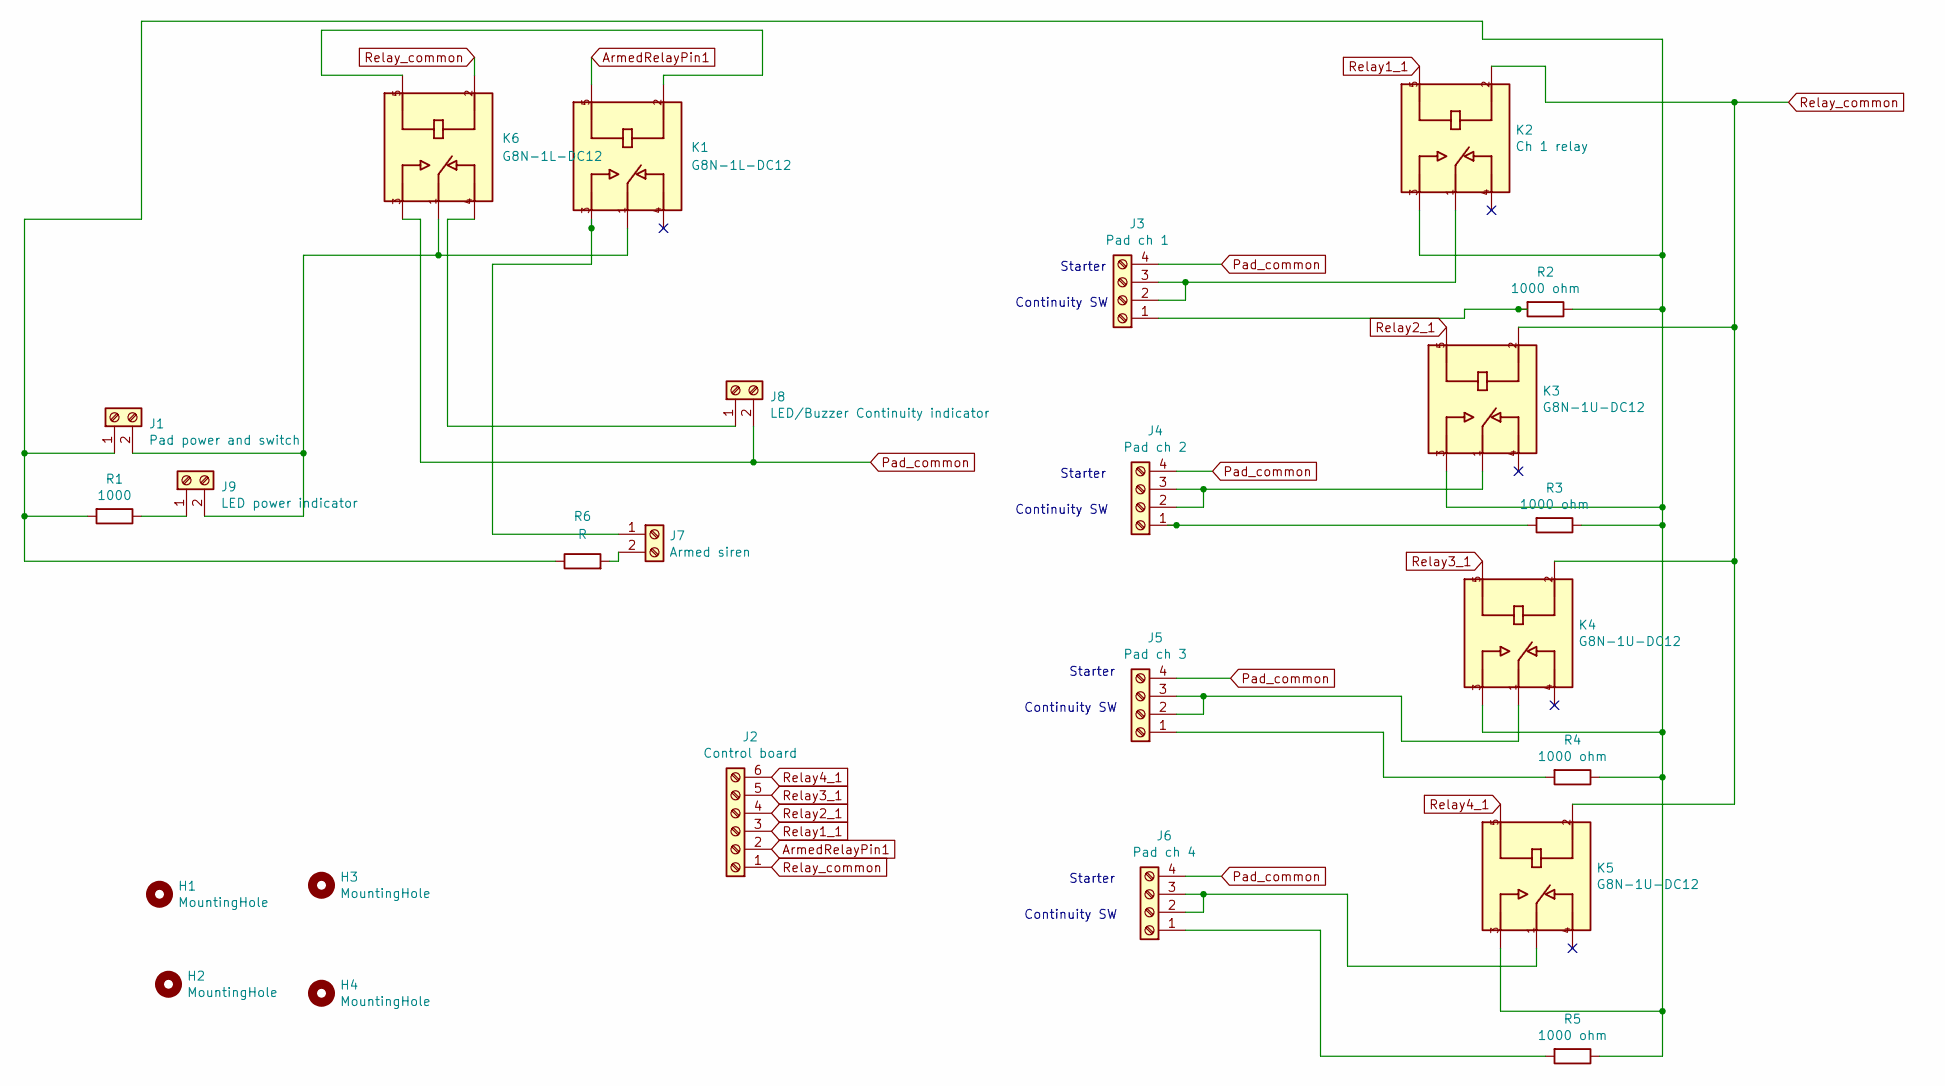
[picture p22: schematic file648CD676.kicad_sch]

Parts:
H1, H2, H3, H4: MountingHole; MountingHole_5.3mm_M5_DIN965_Pad
J1: Pad power and switch; CUI_TB007-508-02BE
J2: Control board; CUI_TB007-508-06BE
J3: Pad ch 1; CUI_TB007-508-04BE
J4: Pad ch 2; CUI_TB007-508-04BE
J5: Pad ch 3; CUI_TB007-508-04BE
J6: Pad ch 4; CUI_TB007-508-04BE
J7: Armed siren; CUI_TB007-508-02BE
J8: LED/Buzzer Continuity indicator; CUI_TB007-508-02BE
J9: LED power indicator; CUI_TB007-508-02BE
K1, K6: G8N-1L-DC12; RELAY_G8N-1U-DC12; PARTREV NA
K2: Ch 1 relay; RELAY_G8N-1U-DC12; PARTREV NA
K3, K4, K5: G8N-1U-DC12; RELAY_G8N-1U-DC12; PARTREV NA
R1: 1000; R_Axial_DIN0207_L6.3mm_D2.5mm_P7.62mm_Horizontal
R2, R3, R4, R5: 1000 ohm; R_Axial_DIN0207_L6.3mm_D2.5mm_P7.62mm_Horizontal
R6: R; R_Axial_DIN0207_L6.3mm_D2.5mm_P7.62mm_Horizontal

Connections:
ArmedRelayPin1: J2.2, K1.5
unnamed: J1.1, K2.3, K3.3, K4.3, K5.3, R1.2, R2.1, R3.1, R4.1, R5.1, R6.1
unnamed: J1.2, J9.2, K1.1, K6.1
unnamed: J3.1, R2.2
unnamed: J3.2, J3.3, K2.1
unnamed: J4.1, R3.2
unnamed: J4.2, J4.3, K3.1
unnamed: J5.1, R4.2
unnamed: J5.2, J5.3, K4.1
unnamed: J6.1, R5.2
unnamed: J6.2, J6.3, K5.1
unnamed: J7.1, K1.3
unnamed: J7.2, R6.2
unnamed: J8.1, K6.4
unnamed: J9.1, R1.1
unnamed: K1.2, K6.5
Pad_common: J3.4, J4.4, J5.4, J6.4, J8.2, K6.3
Relay1_1: J2.3, K2.5
Relay2_1: J2.4, K3.5
Relay3_1: J2.5, K4.5
Relay4_1: J2.6, K5.5
Relay_common: J2.1, K2.2, K3.2, K4.2, K5.2, K6.2

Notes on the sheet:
Continuity SW
Starter

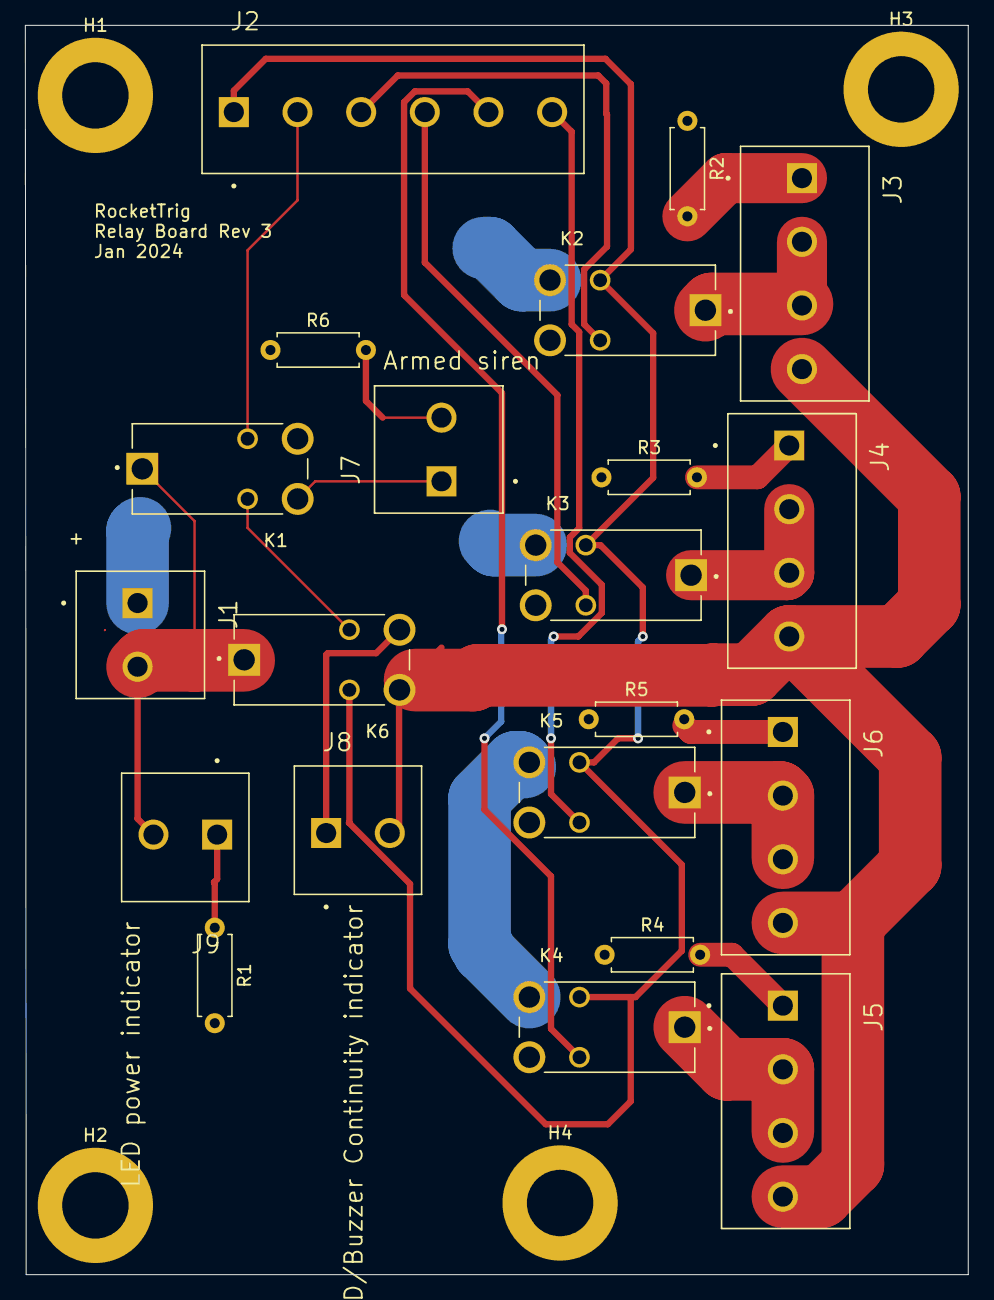
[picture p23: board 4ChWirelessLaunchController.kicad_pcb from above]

Board: 2 copper layers, 75.2 x 99.7 mm, 25 parts (0 on the bottom side), 22 nets.

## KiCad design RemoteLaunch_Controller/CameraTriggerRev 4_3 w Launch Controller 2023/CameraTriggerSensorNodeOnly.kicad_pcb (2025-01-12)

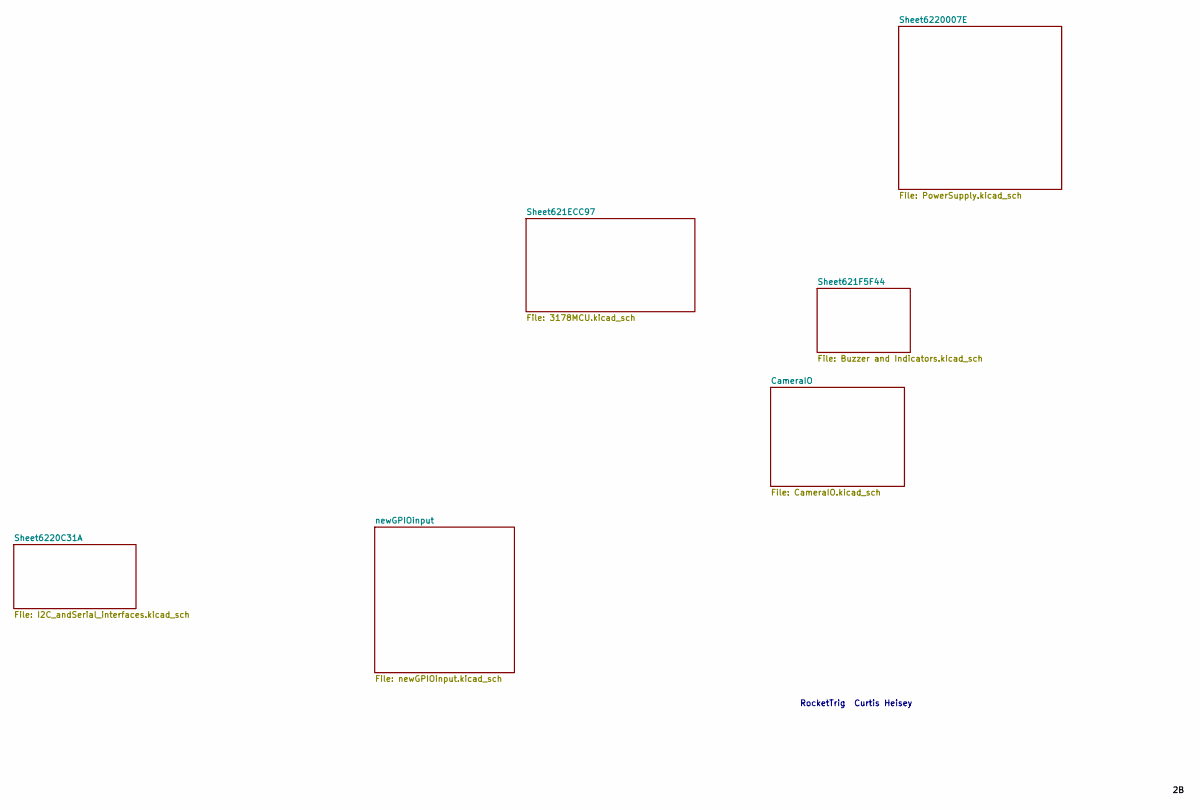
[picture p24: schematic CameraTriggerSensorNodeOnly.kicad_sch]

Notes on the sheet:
RocketTrig Curtis Heisey

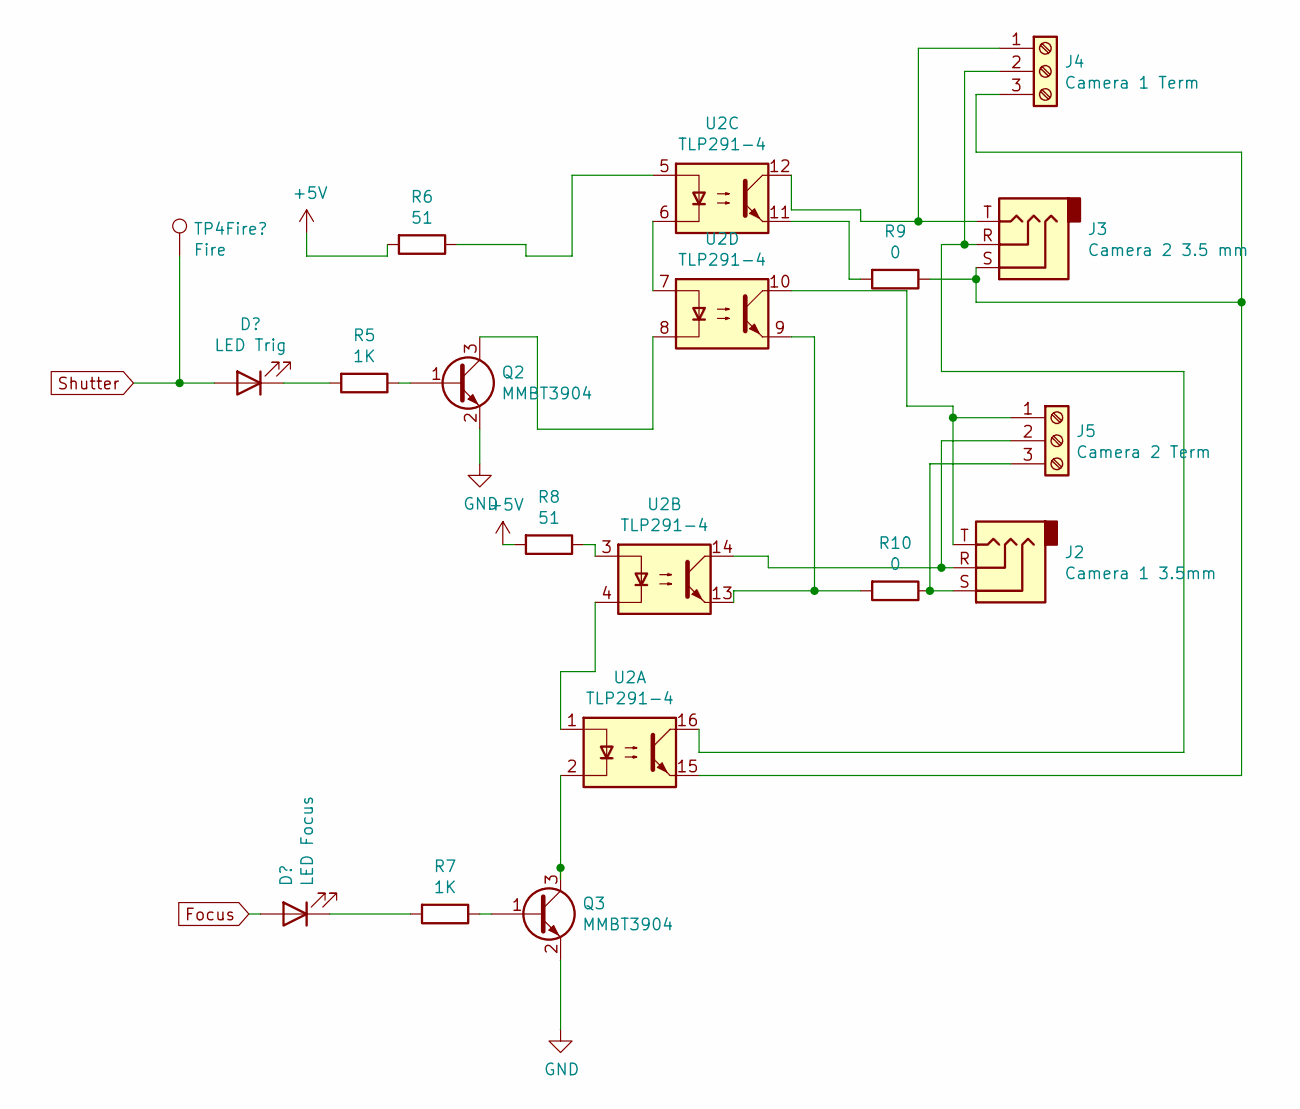
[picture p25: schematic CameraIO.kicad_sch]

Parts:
D4: LED Trig; LED_0805_2012Metric_Castellated
D5: LED Focus; LED_0805_2012Metric_Pad1.15x1.40mm_HandSolder
J2: Camera 1 3.5mm; Jack_3.5mm_CUI_SJ1-3533NG_Horizontal_CircularHoles
J3: Camera 2 3.5 mm; Jack_3.5mm_CUI_SJ1-3533NG_Horizontal_CircularHoles
J4: Camera 1 Term; TerminalBlock_TE_282834-3_1x03_P2.54mm_Horizontal
J5: Camera 2 Term; TerminalBlock_TE_282834-3_1x03_P2.54mm_Horizontal
Q2, Q3: MMBT3904; SOT-23; LCSC C8512
R5, R7: 1K; R_0603_1608Metric; LCSC C22843
R6, R8: 51; R_0603_1608Metric; LCSC C880145
R9, R10: 0; R_0805_2012Metric_Pad1.15x1.40mm_HandSolder; LCSC C17477
TP4Fire1: Fire; TestPoint_Keystone_5010-5014_Multipurpose
U2: TLP291-4; SOIC-16_4.55x10.3mm_P1.27mm; LCSC C60900

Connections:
+5V: R6.2, R8.2; also elsewhere on the board
Focus: D5.2 (A); also elsewhere on the board
GND: Q2.2 (E), Q3.2 (E); also elsewhere on the board
unnamed: D4.1 (K), R5.2
unnamed: D5.1 (K), R7.2
unnamed: J3.T, J4.1, U2.12
unnamed: J3.R, J4.2, U2.16
unnamed: J3.S, J4.3, R9.1, U2.15
unnamed: J2.T, J5.1, U2.10
unnamed: J2.R, J5.2, U2.14
unnamed: J2.S, J5.3, R10.1
unnamed: Q2.1 (B), R5.1
unnamed: Q2.3 (C), U2.8
unnamed: Q3.1 (B), R7.1
unnamed: Q3.3 (C), U2.2
unnamed: R6.1, U2.5
unnamed: R8.1, U2.3
unnamed: R9.2, U2.11
unnamed: R10.2, U2.9, U2.13
unnamed: U2.1, U2.4
unnamed: U2.6, U2.7
Shutter: D4.2 (A), TP4Fire1.1; also elsewhere on the board

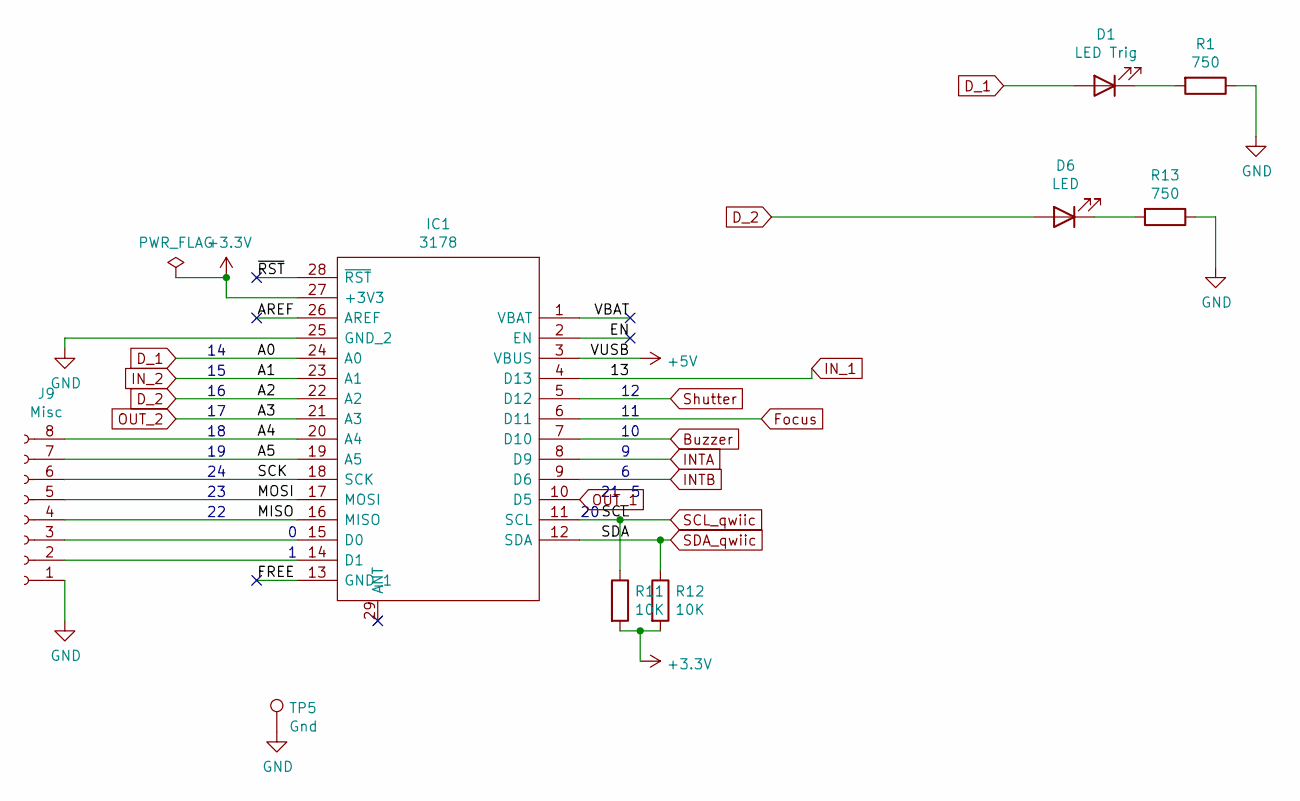
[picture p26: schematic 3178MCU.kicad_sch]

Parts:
D1: LED Trig; LED_0805_2012Metric_Pad1.15x1.40mm_HandSolder
D6: LED; LED_0805_2012Metric_Pad1.15x1.40mm_HandSolder
IC1: 3178; Mouser2 Part Number 485-3178
J9: Misc; PinHeader_1x08_P2.54mm_Vertical
R1, R13: 750; R_0603_1608Metric; LCSC C23241
R11, R12: 10K; R_0603_1608Metric; LCSC C25804
TP5: Gnd; TestPoint_Keystone_5000-5004_Miniature

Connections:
+3V3: IC1.27 (+3V3), J9.9, R11.2, R12.2; also elsewhere on the board
+5V: IC1.3 (VBUS); also elsewhere on the board
/Sheet621ECC97/A4: IC1.20 (A4), J9.8
/Sheet621ECC97/A5: IC1.19 (A5), J9.7
/Sheet621ECC97/AREF: IC1.26 (AREF)
/Sheet621ECC97/EN: IC1.2 (EN)
/Sheet621ECC97/FREE: IC1.13 (GND_1)
/Sheet621ECC97/MISO: IC1.16 (MISO), J9.4
/Sheet621ECC97/MOSI: IC1.17 (MOSI), J9.5
/Sheet621ECC97/SCK: IC1.18 (SCK), J9.6
/Sheet621ECC97/VBAT: IC1.1 (VBAT)
/Sheet621ECC97/~RST: IC1.28 (~RST)
Buzzer: IC1.7 (D10); also elsewhere on the board
D_1: D1.2 (A), IC1.24 (A0)
D_2: D6.2 (A), IC1.22 (A2)
Focus: IC1.6 (D11); also elsewhere on the board
GND: IC1.25 (GND_2), J9.1, R1.1, R13.1, TP5.1; also elsewhere on the board
INTA: IC1.8 (D9); also elsewhere on the board
INTB: IC1.9 (D6); also elsewhere on the board
IN_1: IC1.4 (D13); also elsewhere on the board
IN_2: IC1.23 (A1); also elsewhere on the board
unnamed: D1.1 (K), R1.2
unnamed: D6.1 (K), R13.2
unnamed: IC1.15 (D0), J9.3
unnamed: IC1.14 (D1), J9.2
OUT_1: IC1.10 (D5); also elsewhere on the board
OUT_2: IC1.21 (A3); also elsewhere on the board
SCL_qwiic: IC1.11 (SCL), R11.1; also elsewhere on the board
SDA_qwiic: IC1.12 (SDA), R12.1; also elsewhere on the board
Shutter: IC1.5 (D12); also elsewhere on the board

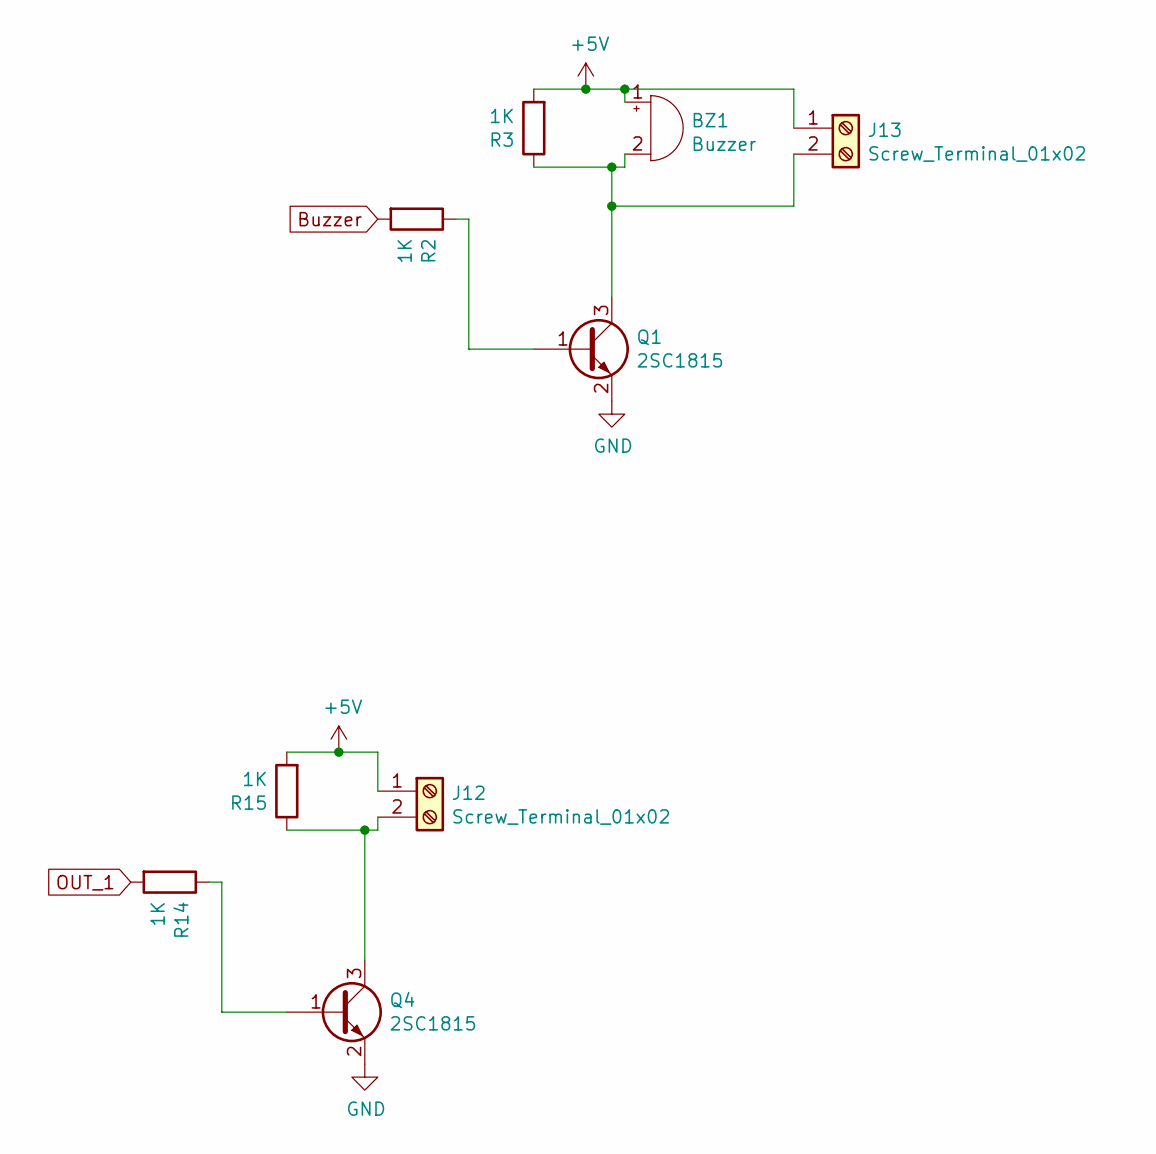
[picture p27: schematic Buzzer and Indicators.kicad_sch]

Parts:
BZ1: Buzzer; Buzzer_TDK_PS1240P02BT_D12.2mm_H6.5mm
J12, J13: Screw_Terminal_01x02; TerminalBlock_TE_282834-2_1x02_P2.54mm_Horizontal
Q1, Q4: 2SC1815; SOT-23; LCSC C181171
R2, R3, R14, R15: 1K; R_0603_1608Metric; LCSC C21190

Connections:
+5V: BZ1.1 (-), J12.1, J13.1, R3.2, R15.2; also elsewhere on the board
Buzzer: R2.2; also elsewhere on the board
GND: Q1.2 (E), Q4.2 (E); also elsewhere on the board
unnamed: BZ1.2 (+), J13.2, Q1.3 (C), R3.1
unnamed: J12.2, Q4.3 (C), R15.1
unnamed: Q1.1 (B), R2.1
unnamed: Q4.1 (B), R14.1
OUT_1: R14.2; also elsewhere on the board

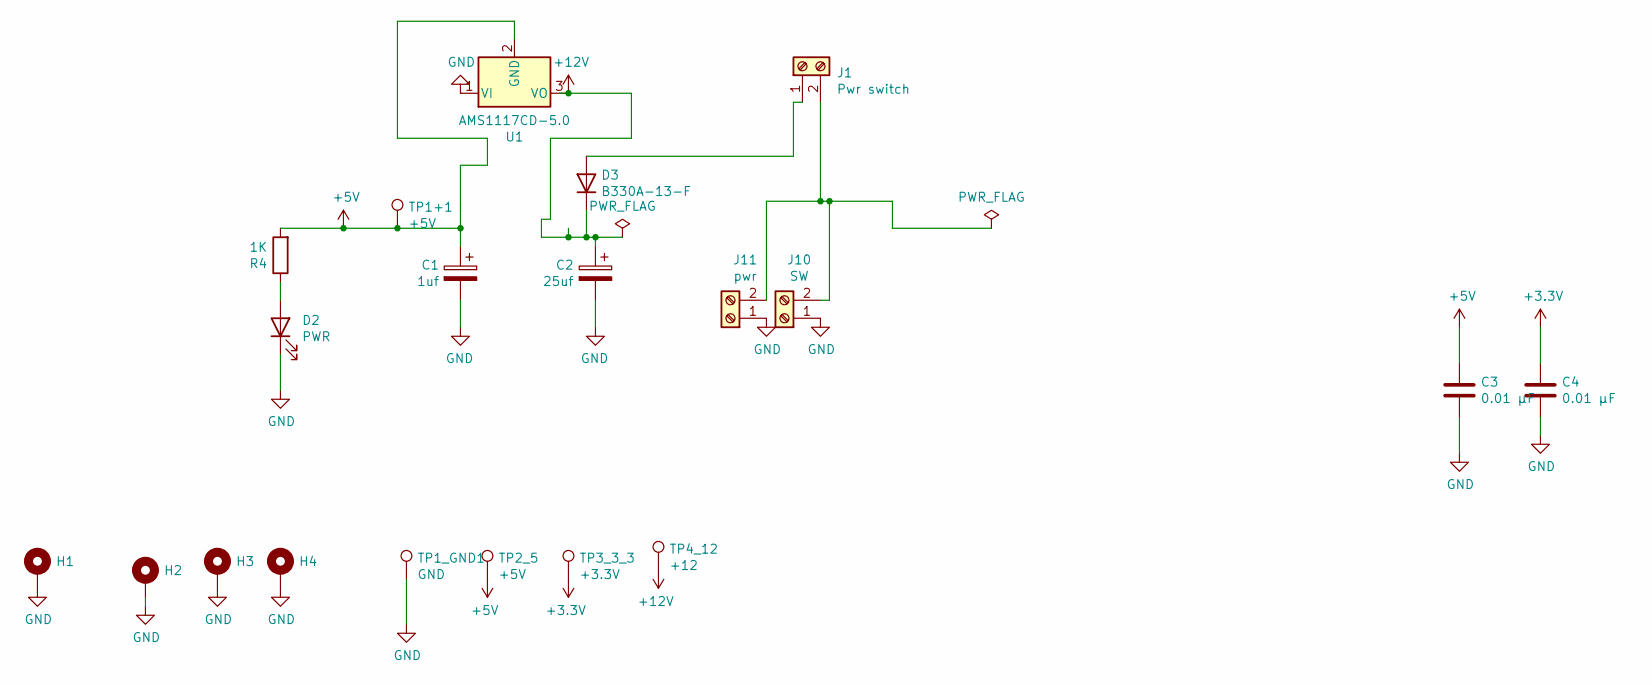
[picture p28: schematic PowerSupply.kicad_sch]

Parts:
C1: 1uf; CP_Elec_4x5.4; LCSC C87863
C2: 25uf; C_Elec_4x5.4; LCSC C2895283
C3, C4: 0.01 μF; C_0402_1005Metric; LCSC C1525
D2: PWR; LED_0603_1608Metric; LCSC C2286
D3: B330A-13-F; D_SMA; LCSC C110485
H1, H2, H3, H4: MountingHole_3.7mm_Pad
J1: Pwr switch; CUI_TB007-508-02BE
J10: SW; AMASS_XT30U-F_1x02_P5.0mm_Vertical
J11: pwr; CUI_TB007-508-02BE
R4: 1K; R_0603_1608Metric; LCSC C21190
TP1+1, TP2_5: +5V; TestPoint_Keystone_5010-5014_Multipurpose
TP1_GND1: GND; TestPoint_Keystone_5010-5014_Multipurpose
TP3_3_3: +3.3V; TestPoint_Keystone_5010-5014_Multipurpose
TP4_12: +12; TestPoint_Keystone_5010-5014_Multipurpose
U1: AMS1117CD-5.0; SOT-223; LCSC C6187

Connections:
+3V3: C4.1, TP3_3_3.1; also elsewhere on the board
+5V: C1.1, C3.1, R4.2, TP1+1.1, TP2_5.1, U1.2 (GND); also elsewhere on the board
+12V: C2.1, D3.1 (K), TP4_12.1, U1.3 (VO); also elsewhere on the board
GND: C1.2, C2.2, C3.2, C4.2, D2.1 (K), H1.1, H2.1, H3.1, H4.1, J10.1, J11.1, TP1_GND1.1, U1.1 (VI); also elsewhere on the board
unnamed: D2.2 (A), R4.1
unnamed: D3.2 (A), J1.1
unnamed: J1.2, J10.2, J11.2

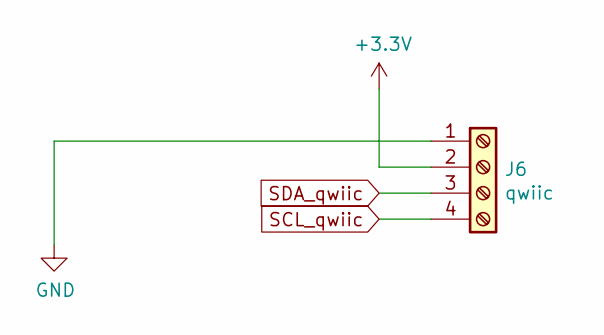
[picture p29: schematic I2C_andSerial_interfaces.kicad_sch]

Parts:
J6: qwiic; JST_SH_SM04B-SRSS-TB_1x04-1MP_P1.00mm_Horizontal; LCSC C160404

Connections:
+3V3: J6.2; also elsewhere on the board
GND: J6.1; also elsewhere on the board
SCL_qwiic: J6.4; also elsewhere on the board
SDA_qwiic: J6.3; also elsewhere on the board

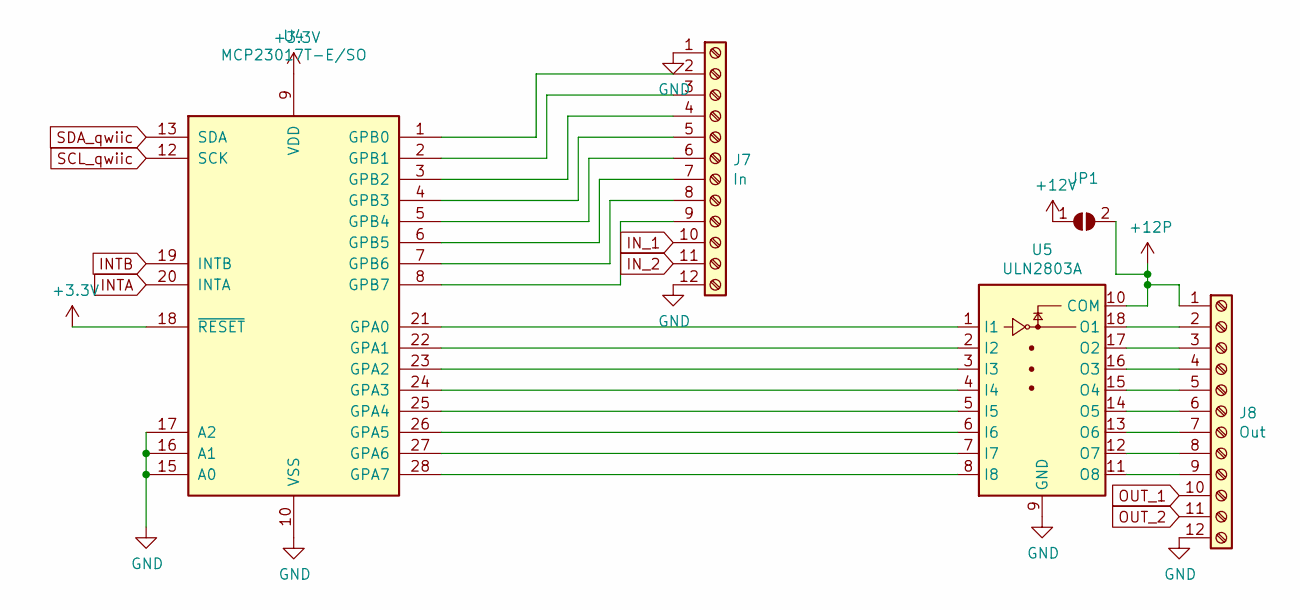
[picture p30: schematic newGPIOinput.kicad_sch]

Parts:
J7: In; TB00750812BE
J8: Out; TB00750812BE
JP1: SolderJumper-2_P1.3mm_Open_TrianglePad1.0x1.5mm
U4: MCP23017T-E/SO; SOIC-28W_7.5x17.9mm_P1.27mm; LCSC C629440
U5: ULN2803A; SOIC127P1030X265-18N; LCSC C9683

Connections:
+3V3: U4.9 (VDD), U4.18 (~RESET); also elsewhere on the board
+12P: J8.1, JP1.2 (B), U5.10 (COM)
+12V: JP1.1 (A); also elsewhere on the board
GND: J7.1, J7.12, J8.12, U4.10 (VSS), U4.15 (A0), U4.16 (A1), U4.17 (A2), U5.9 (GND); also elsewhere on the board
INTA: U4.20 (INTA); also elsewhere on the board
INTB: U4.19 (INTB); also elsewhere on the board
IN_1: J7.10; also elsewhere on the board
IN_2: J7.11; also elsewhere on the board
unnamed: J7.2, U4.1 (GPB0)
unnamed: J7.3, U4.2 (GPB1)
unnamed: J7.4, U4.3 (GPB2)
unnamed: J7.5, U4.4 (GPB3)
unnamed: J7.6, U4.5 (GPB4)
unnamed: J7.7, U4.6 (GPB5)
unnamed: J7.8, U4.7 (GPB6)
unnamed: J7.9, U4.8 (GPB7)
unnamed: J8.2, U5.18 (O1)
unnamed: J8.3, U5.17 (O2)
unnamed: J8.4, U5.16 (O3)
unnamed: J8.5, U5.15 (O4)
unnamed: J8.6, U5.14 (O5)
unnamed: J8.7, U5.13 (O6)
unnamed: J8.8, U5.12 (O7)
unnamed: J8.9, U5.11 (O8)
unnamed: U4.21 (GPA0), U5.1 (I1)
unnamed: U4.22 (GPA1), U5.2 (I2)
unnamed: U4.23 (GPA2), U5.3 (I3)
unnamed: U4.24 (GPA3), U5.4 (I4)
unnamed: U4.25 (GPA4), U5.5 (I5)
unnamed: U4.26 (GPA5), U5.6 (I6)
unnamed: U4.27 (GPA6), U5.7 (I7)
unnamed: U4.28 (GPA7), U5.8 (I8)
OUT_1: J8.10; also elsewhere on the board
OUT_2: J8.11; also elsewhere on the board
SCL_qwiic: U4.12 (SCK); also elsewhere on the board
SDA_qwiic: U4.13 (SDA); also elsewhere on the board

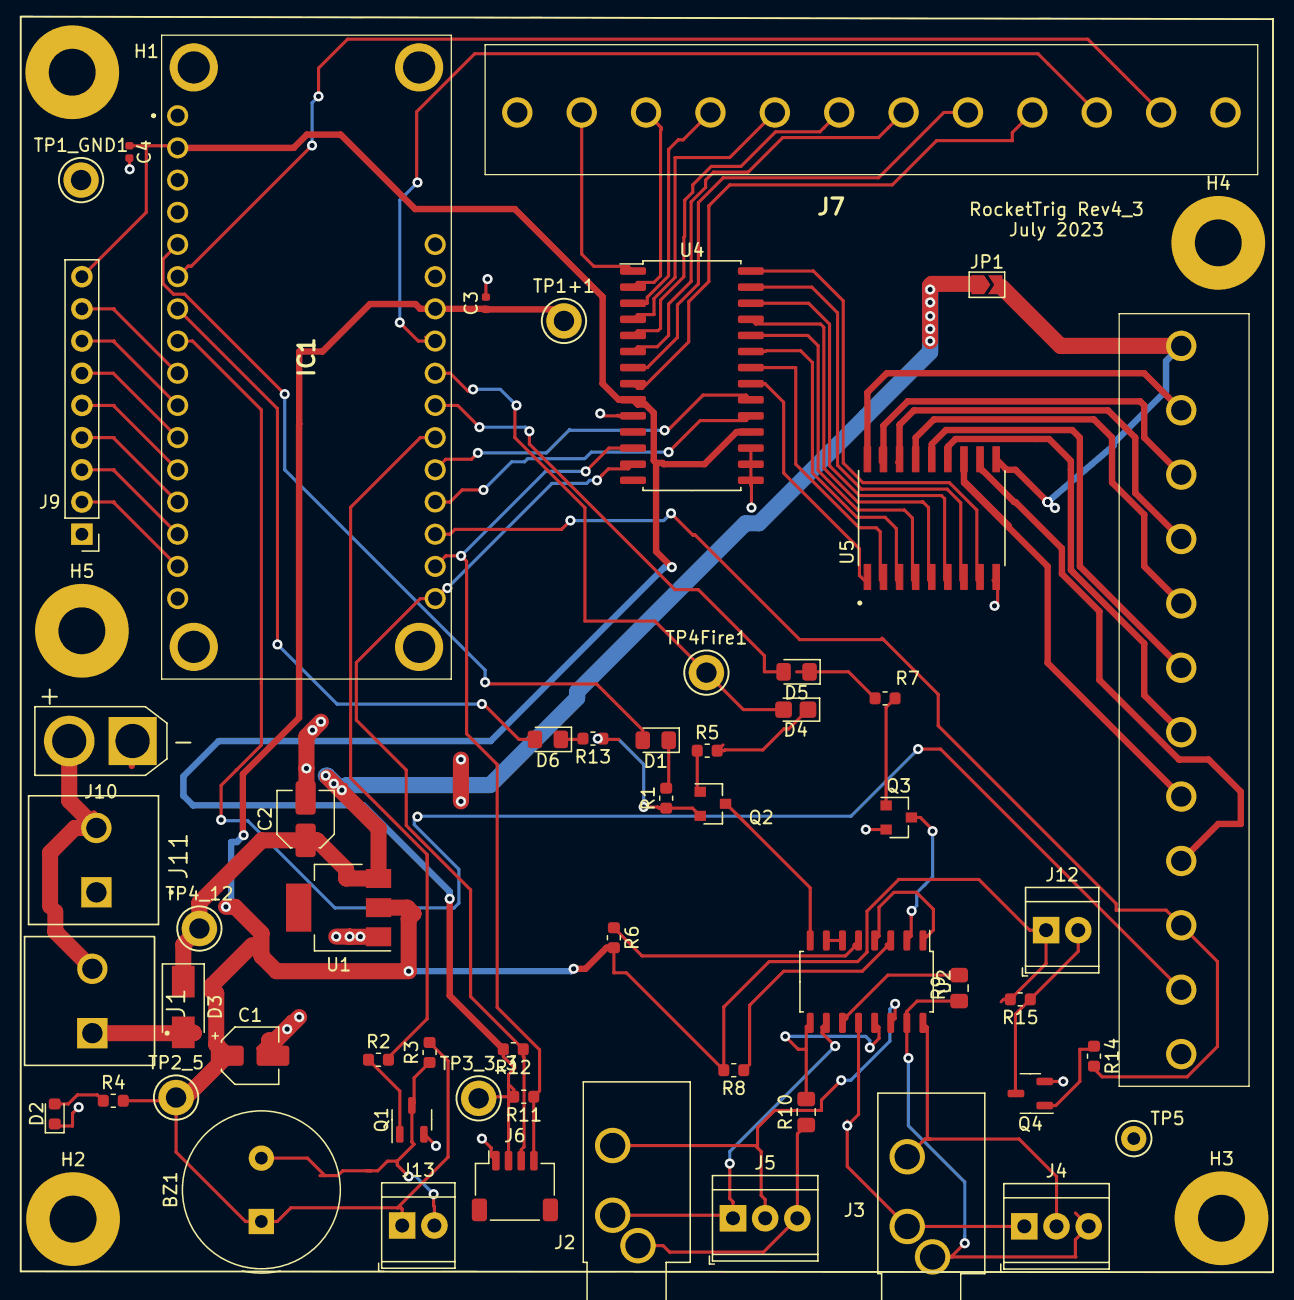
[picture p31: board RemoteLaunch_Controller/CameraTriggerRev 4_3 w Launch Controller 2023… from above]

Board: 2 copper layers, 61 parts (0 on the bottom side), 76 nets.

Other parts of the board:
H5: MountingHole_3.7mm_Pad

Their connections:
GND: H5.1; also elsewhere on the board

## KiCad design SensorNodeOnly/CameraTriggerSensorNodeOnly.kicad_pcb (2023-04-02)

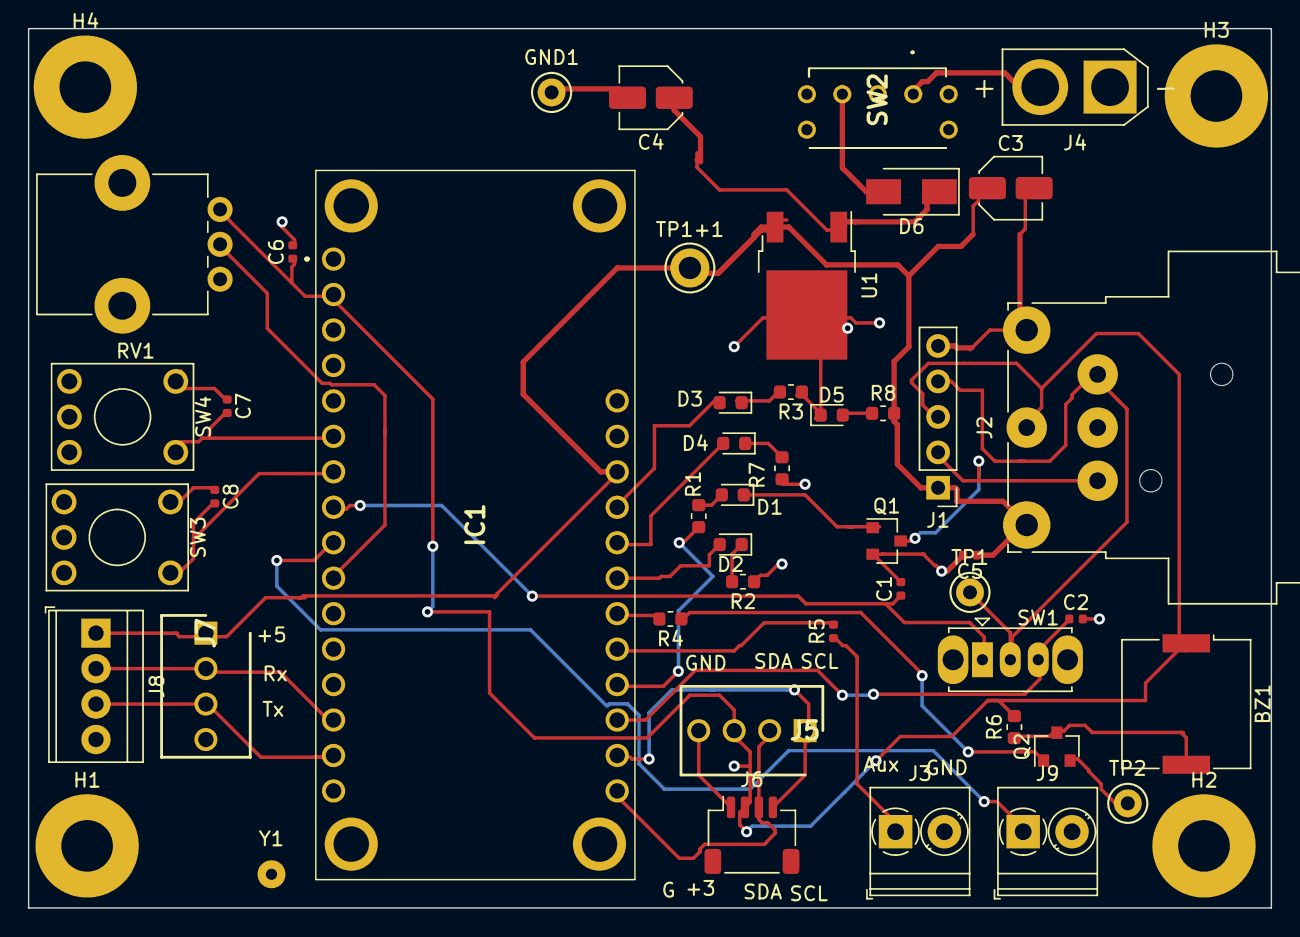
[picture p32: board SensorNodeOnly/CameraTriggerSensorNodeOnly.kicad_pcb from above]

Board: 2 copper layers, 89.0 x 63.0 mm, 50 parts (0 on the bottom side), 33 nets.

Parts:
BZ1: Buzzer; Buzzer_Murata_PKMCS0909E4000-R1
C1, C2, C5, C6, C7, C8: 0.01 μF; C_0402_1005Metric
C3: 1uf; C_Elec_4x5.4
C4: 25uf; C_Elec_4x5.4
D1: Arm; LED_0603_1608Metric
D2: Trig2; LED_0603_1608Metric
D3: Trig1; LED_0603_1608Metric
D4: Shutter; LED_0603_1608Metric
D5: PWR; LED_0603_1608Metric
D6: SR560-T; D_SMA
GND1: TestPoint; TestPoint_Keystone_5000-5004_Miniature
H1, H2, H3, H4: MountingHole_3.7mm_Pad
IC1: 3178
J1: PinHeader_1x05_P2.54mm_Vertical
J2: XLR5 Male; Jack_XLR_Neutrik_NC5MBH_Horizontal
J3: Aux out; TerminalBlock_Phoenix_PT-1,5-2-3.5-H_1x02_P3.50mm_Horizontal
J4: AMASS_XT30U-F_1x02_P5.0mm_Vertical
J5: HDRV4W64P0X254_1X4_1016X635X1067P
J6: I2C; JST_SH_SM04B-SRSS-TB_1x04-1MP_P1.00mm_Horizontal
J7: Conn_01x04_Male; HDRV4W64P0X254_1X4_1016X635X1067P
J8: Serial; TerminalBlock_TE_282834-4_1x04_P2.54mm_Horizontal
J9: Analog in; TerminalBlock_Phoenix_PT-1,5-2-3.5-H_1x02_P3.50mm_Horizontal
Q1: MMBT3904; SOT-23
Q2: 2SC1815; SOT-23
R1, R2, R3, R4, R6, R7, R8: 1K; R_0603_1608Metric
R5: 5K; R_0402_1005Metric
RV1: 1K; Potentiometer_Alps_RK09K_Single_Vertical
SW1: SW_Slide_1P2T_CK_OS102011MS2Q
SW2: AS11CB
SW3: SW_Poll; KSA_Tactile_SPST
SW4: SW_Arm; KSA_Tactile_SPST
TP1: Sensor; TestPoint_Keystone_5000-5004_Miniature
TP1+1: +5V; TestPoint_Keystone_5010-5014_Multipurpose
TP2: Gnd; TestPoint_Keystone_5000-5004_Miniature
U1: LM7805_TO220; TO-252-2
Y1: SolderWirePad_1x01_Drill0.8mm

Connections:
+3V3: BZ1.1, C6.1, IC1.27, J1.3, J2.3, J5.3, J6.2, R6.2, RV1.1
+5V: C3.1, C5.1, IC1.3, J1.1, J2.1, J7.1, J8.1, R8.2, TP1+1.1, U1.3
+7.5V: J4.2, SW2.1
/Sheet621ECC97/13: D3.2, IC1.4
ANALOG_IN: IC1.20, J9.1
ArmIn: C7.2, IC1.23, SW4.2
ArmInd: IC1.9, R1.2
AuxIn: C1.1, IC1.21, SW1.1
AuxOut: IC1.8, R5.2
Buzzer: IC1.7, R4.2
GND: C1.2, C2.2, C3.2, C4.2, C5.2, C6.2, C7.1, C8.1, D5.1, GND1.1, H1.1, H2.1, H3.1, H4.1, IC1.25, J1.5, J2.5, J3.2, J4.1, J5.4, J6.1, J7.4, J8.4, J9.2, Q1.2, Q2.2, R2.1, R3.1, R7.1, RV1.3, SW3.1, SW4.1, TP2.1, U1.2
Laser: J1.2, J2.2, Q1.3
unnamed: BZ1.2, Q2.3, R6.1
unnamed: C4.1, D6.1, U1.1
unnamed: D1.1, Q1.1
unnamed: D1.2, R1.1
unnamed: D2.1, R2.2
unnamed: D2.2, IC1.6
unnamed: D3.1, R3.2
unnamed: D4.1, R7.2
unnamed: D5.2, R8.1
unnamed: D6.2, SW2.3
unnamed: J1.4, J2.4, SW1.2, TP1.1
unnamed: J3.1, R5.1
unnamed: Q2.1, R4.1
Poll: C8.2, IC1.22, SW3.2
Rx_serial: IC1.15, J7.2, J8.2
SCL_qwiic: IC1.11, J5.1, J6.4
SDA_qwiic: IC1.12, J5.2, J6.3
SensorIn: C2.1, IC1.10, SW1.3
Shutter: D4.2, IC1.5
Threshold: IC1.19, RV1.2
Tx_serial: IC1.14, J7.3, J8.3

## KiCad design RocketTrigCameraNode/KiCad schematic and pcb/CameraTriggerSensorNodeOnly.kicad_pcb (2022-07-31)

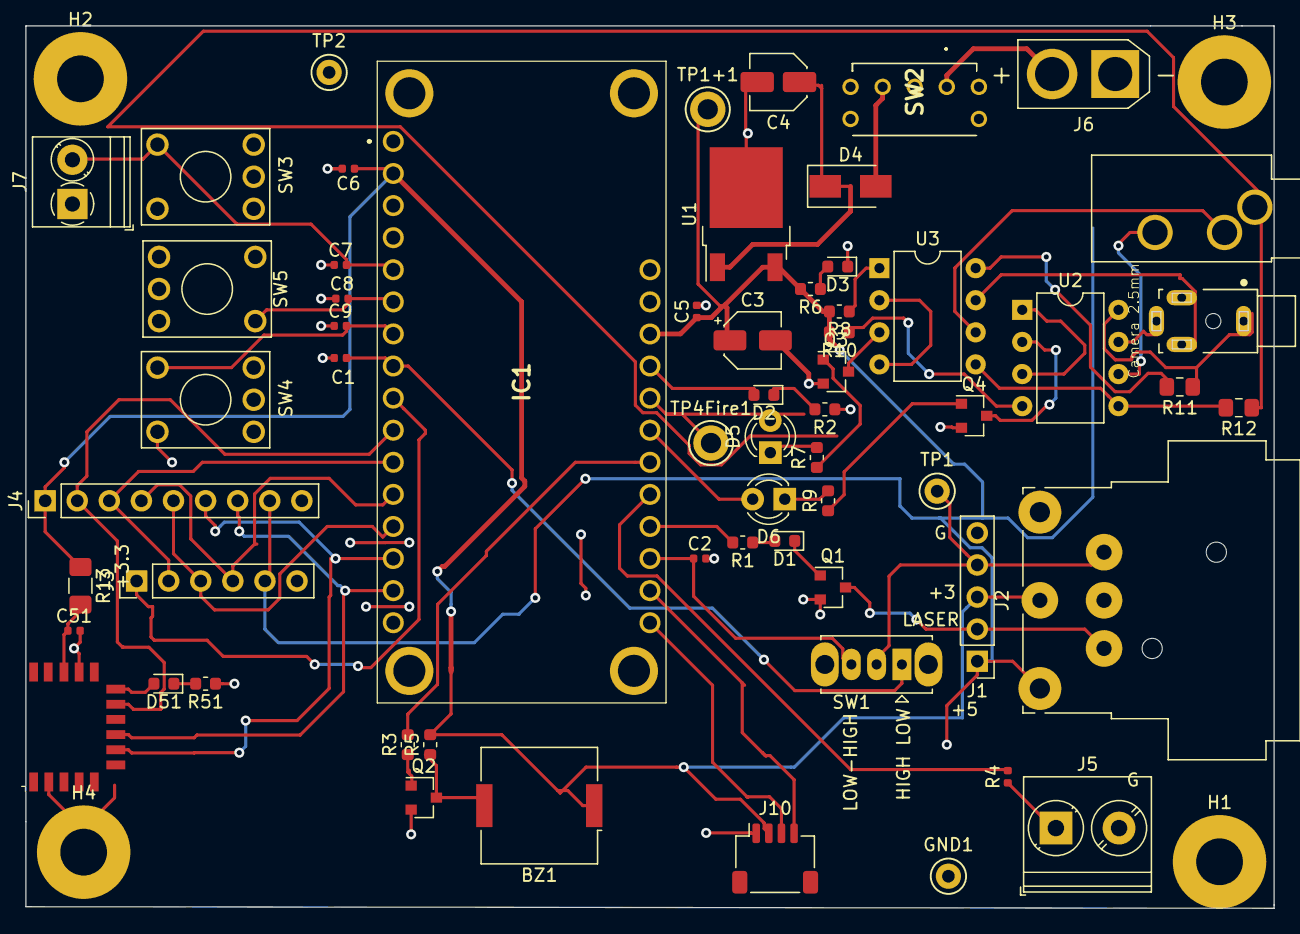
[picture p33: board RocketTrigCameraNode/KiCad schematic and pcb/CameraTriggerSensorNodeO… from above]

Board: 2 copper layers, 98.8 x 69.9 mm, 65 parts (0 on the bottom side), 56 nets.

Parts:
BZ1: Buzzer; Buzzer_Murata_PKMCS0909E4000-R1
C1, C2, C5, C6, C7, C8, C9: 0.01 μF; C_0402_1005Metric
C3: 1uf; CP_Elec_4x5.4
C4: 25uf; C_Elec_4x5.4
C51: 100n; C_0402_1005Metric
D1: LED Arm; LED_0603_1608Metric
D2: LED Trig; LED_0603_1608Metric
D3: PWR; LED_0603_1608Metric
D4: B330A-13-F; D_SMA
D5: LED Trig; LED_D3.0mm
D6: LED Focus; LED_D3.0mm
D51: BLUE; LED_0603_1608Metric
GND1: TestPoint; TestPoint_Keystone_5000-5004_Miniature
H1, H2, H3, H4: MountingHole_3.7mm_Pad
IC1: 3178
J1: PinHeader_1x05_P2.54mm_Vertical
J2: XLR5 Male; Jack_XLR_Neutrik_NC5MBH_Horizontal
J3: PinHeader_1x06_P2.54mm_Vertical
J4: PinHeader_1x09_P2.54mm_Vertical
J5: Aux out; TerminalBlock_Phoenix_PT-1,5-2-5.0-H_1x02_P5.00mm_Horizontal
J6: AMASS_XT30U-F_1x02_P5.0mm_Vertical
J7: Trig in; TerminalBlock_Phoenix_PT-1,5-2-3.5-H_1x02_P3.50mm_Horizontal
J8: Camera 3.5mm; Jack_3.5mm_CUI_SJ1-3533NG_Horizontal_CircularHoles
J9: Camera 2.5mm; CUI_SJ1-2503A
J10: qwiic; JST_SH_SM04B-SRSS-TB_1x04-1MP_P1.00mm_Horizontal
Q1, Q3, Q4: MMBT3904; SOT-23
Q2: 2SC1815; SOT-23
R1, R2, R3, R5, R6, R7, R9: 1K; R_0603_1608Metric
R4: 5K; R_0402_1005Metric
R8, R10: 51; R_0603_1608Metric
R11, R12: 0; R_0805_2012Metric_Pad1.15x1.40mm_HandSolder
R13: 0; R_1206_3216Metric_Pad1.42x1.75mm_HandSolder
R51: 1k5; R_0603_1608Metric
SW1: SW_Slide_1P2T_CK_OS102011MS2Q
SW2: AS11CB
SW3: SW_trig; KSA_Tactile_SPST
SW4: SW_Poll; KSA_Tactile_SPST
SW5: SW_Arm; KSA_Tactile_SPST
TP1: Sensor; TestPoint_Keystone_5000-5004_Miniature
TP1+1: +5V; TestPoint_Keystone_5010-5014_Multipurpose
TP2: Gnd; TestPoint_Keystone_5000-5004_Miniature
TP4Fire1: Fire; TestPoint_Keystone_5010-5014_Multipurpose
U1: LM7805_TO220; TO-252-2
U2, U3: ILD74; DIP-8_W7.62mm
U5: RN4871; Microchip_RN4871

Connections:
+3V3: BZ1.1, C6.1, IC1.27, J1.3, J2.3, J4.1, J10.2, R5.2, R13.1
+5V: C3.1, C5.1, IC1.3, J1.1, J2.1, J3.5, J4.8, R6.2, R8.2, R10.2, TP1+1.1, U1.3
+7.5V: J6.2, SW2.1
/Sheet621ECC97/13: D2.2, IC1.4
/Sheet621ECC97/A4: IC1.20, J3.1
/Sheet621ECC97/MISO: IC1.16, J3.3, J4.5
/Sheet621ECC97/MOSI: IC1.17, J3.4, J4.4
/Sheet621ECC97/SCK: IC1.18, J3.2, J4.3
ArmIn: C8.2, IC1.23, SW5.2
ArmInd: IC1.9, R1.2
AuxIn: C1.1, IC1.21, SW1.1
AuxOut: IC1.8, R4.2
BLE_reset: IC1.19, J4.2, U5.10
Buzzer: IC1.7, R3.2
Focus: D6.2, IC1.6
GND: C1.2, C2.2, C3.2, C4.2, C5.2, C6.2, C7.1, C8.1, C9.1, C51.2, D3.1, GND1.1, H1.1, H2.1, H3.1, H4.1, IC1.25, J1.5, J2.5, J3.6, J4.9, J5.2, J6.1, J7.1, J10.1, Q1.2, Q2.2, Q3.2, Q4.2, R2.1, R51.1, SW3.1, SW4.1, SW5.1, TP2.1, U1.2, U5.2, U5.13
LED_TXRX: D51.2, U5.11
Laser: J1.2, J2.2, Q1.3
unnamed: BZ1.2, Q2.3, R5.1
unnamed: C4.1, D4.1, U1.1
unnamed: C51.1, R13.2, U5.14
unnamed: D1.1, Q1.1
unnamed: D1.2, R1.1
unnamed: D2.1, R2.2
unnamed: D3.2, R6.1
unnamed: D4.2, SW2.3
unnamed: D5.1, R7.2
unnamed: D6.1, R9.2
unnamed: D51.1, R51.2
unnamed: J1.4, J2.4, SW1.2, TP1.1
unnamed: J5.1, R4.1
unnamed: J8.R, U2.6
unnamed: J8.S, R12.1
unnamed: J8.T, U3.6
unnamed: J9.R, U2.7
unnamed: J9.S, R11.1, U2.8
unnamed: J9.T, U3.7
unnamed: Q2.1, R3.1
unnamed: Q3.1, R7.1
unnamed: Q3.3, U3.3
unnamed: Q4.1, R9.1
unnamed: Q4.3, U2.2
unnamed: R8.1, U3.1
unnamed: R10.1, U2.4
unnamed: R11.2, U3.8
unnamed: R12.2, U2.5, U3.5
unnamed: U2.1, U2.3
unnamed: U3.2, U3.4
PbTrigIn: C7.2, IC1.24, J7.2, SW3.2
Poll: C9.2, IC1.22, SW4.2
SCL_qwiic: IC1.11, J10.4
SDA_qwiic: IC1.12, J10.3
SensorIn: C2.1, IC1.10, SW1.3
Shutter: D5.2, IC1.5, TP4Fire1.1
UART1_RX: IC1.14, J4.7, U5.8
UART1_TX: IC1.15, J4.6, U5.7

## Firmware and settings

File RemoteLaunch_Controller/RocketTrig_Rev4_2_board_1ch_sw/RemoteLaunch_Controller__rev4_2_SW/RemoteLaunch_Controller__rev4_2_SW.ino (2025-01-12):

// rf65/rf95 (lora) RocketTrigradioSendFireCommand
// This version is a 1ch remote launcher using Rev 4_2 boar

// Last mofidifed 8/5/2024 11:21AM



// Connections
// J7 position 2 - arm pushbutton
// J7 position 3 - clear pushbutton
// J7 position 4 - fire pushbutton
// J7 podiyion 6 - local (launch fire) /remote (sensor in) camera trigger
//
// J8 position 2  - LED armed indicator
// J8 position 3 - fire relay
// J8 position 4 - remote node in contact (poll received)

#include <Wire.h>
//MCP23017 lib by Bertand Lemasle - install using Arduino IDE library manager
#include <MCP23017.h>



// https://github.com/chrocket/RemoteCameraTrigger
// By Curtis Heisey
// For use with Adafruit 3176 (RFM69( or Adafruit 3178 (LoRo RFM95) Feather M0 Packet radio modules
//  SX1276 LoRa®
//
// Requires RadioHead libs - - install using Arduino IDE library manager
// https://www.airspayce.com/mikem/arduino/RadioHead/index.html
// Using ver 1.122.1  http://www.airspayce.com/mikem/arduino/RadioHead/RadioHead-1.122.zip
#include <RadioHead.h>

// Other libs
//CRC32 by Christopher Baker  - install using Arduino IDE library manager
#include <CRC32.h>
// https://github.com/bakercp/CRC32/blob/master/examples/CRC32/CRC32.ino

// But ensure you have installed the Crypto directory from arduinolibs first:
// http://rweather.github.io/arduinolibs/index.html

#undef DEBUG

#define MCP23017_ADDR 0x20
MCP23017 mcp = MCP23017(MCP23017_ADDR);

#if defined(ARDUINO_SAMD_ZERO) && defined(SERIAL_PORT_USBVIRTUAL)
// Required for Serial on Zero based boards
#define Serial SERIAL_PORT_USBVIRTUAL
#endif


// pin assignments
const unsigned int BUZZER_OUT_PIN = 10;          // Pin to audible indicator
const unsigned int CAMERA_TRIGGER_OUT_PIN = 12;  // Pin for shtter opto-isoloatr
const unsigned int CAMERA_FOCUS_OUT_PIN = 11;    // Pin for focus opto-isolator
const unsigned int LED_OUT_PIN = 13;
const unsigned int ARM_OUT_PIN = 0;                 //MCP23017Pin::GPA0
const unsigned int RELAY_OUT_PIN = 1;               //MCP23017Pin::GPA1
const unsigned int REMOTE_NODE_IN_CONTACT_LED = 2;  //MCP23017Pin::GPA2
const unsigned int FIRE_INDICATOR_OUT_PIN = 24;
const unsigned int ARM_INDICATOR_OUT_PIN = 22;
const unsigned int OUT_1 = 10;
const unsigned int OUT_2 = 17;


// Radio module stuff
// Pick one module of the other

// #define MODULE_RFM69
// #undef MODULE_RFM95

#undef MODULE_RFM69
#define MODULE_RFM95

#include <SPI.h>


#define RFM69_CS 8
#define RFM69_INT 3
#define RFM69_RST 4
#define LED_PIN 13

// Singleton instance of the radio driver
#if defined(MODULE_RFM69)


#include <RH_RF69.h>
RH_RF69 radio_m0(RFM69_CS, RFM69_INT);  // Adafruit 3176
#define MAX_MESSAGE_LEN RH_RF69_MAX_MESSAGE_LEN
#else
#include <RH_RF95.h>
#define RFM95_CS 8
#define RFM95_RST 4
#define RFM95_INT 3
RH_RF95 radio_m0(RFM95_CS, RFM95_INT);  // Adafruit 3178
#define MAX_MESSAGE_LEN RH_RF95_MAX_MESSAGE_LEN
#endif

// ISM 33cm band USA 902-928 MHZ
#define FREQ 915.3
#define RF95_FREQ FREQ
#define RF69_FREQ FREQ



/*
 * NonBlockingTimer CLASS DEFINITION
 */
class NonBlockingTimer {
protected:
  bool isPressed = LOW;
  unsigned long timeFireOn;
  unsigned long nextChangeTime = 0;
private:
  NonBlockingTimer(){};
public:
  NonBlockingTimer(unsigned int timeFireOnIn) {
    timeFireOn = timeFireOnIn;
  }
  void fire() {
    isPressed = HIGH;
    unsigned long currentTime = millis();
    nextChangeTime = currentTime + timeFireOn;
  }
  bool check() {
    unsigned long currentTime = millis();
    if (currentTime >= nextChangeTime) {
      isPressed = LOW;
    }

    return isPressed;
  }
  bool isBPressed() {
    return isPressed;
  }
  void clear() {
    unsigned long currentTime = millis();
    nextChangeTime = currentTime;
    isPressed = LOW;
  }
  void init() {

    nextChangeTime = 4294967294;
  }
};


/*
 * FireTimer CLASS DEFINITION
 */
class FireTimer : public NonBlockingTimer {
private:
  byte pinLED;

public:
  FireTimer(byte pinLED, unsigned long timeLedOn)
    : NonBlockingTimer(timeLedOn) {
    this->pinLED = pinLED;
    pinMode(pinLED, OUTPUT);
    digitalWrite(pinLED, LOW);
    isPressed = LOW;
  }
  void fire() {
    isPressed = HIGH;
    digitalWrite(pinLED, isPressed);
    unsigned long currentTime = millis();
    nextChangeTime = currentTime + timeFireOn;
  }


  // Checks whether it is time to turn on or off the Output
  bool check() {
    unsigned long currentTime = millis();
    if (currentTime >= nextChangeTime) {
      // Turn output off when time expires
      isPressed = LOW;
    }
    digitalWrite(pinLED, isPressed);
    return isPressed;
  }
};




void printChipId(char *buf) {
  volatile uint32_t val1, val2, val3, val4;
  volatile uint32_t *ptr1 = (volatile uint32_t *)0x0080A00C;
  val1 = *ptr1;
  volatile uint32_t *ptr = (volatile uint32_t *)0x0080A040;
  val2 = *ptr;
  ptr++;
  val3 = *ptr;
  ptr++;
  val4 = *ptr;
  sprintf(buf, "%8x%8x%8x%8x", val1, val2, val3, val4);
}

char myId[3] = { 'a', 'b', 'c' };
// Dont put this on the stack:
uint8_t buf[MAX_MESSAGE_LEN];
//uint8_t buf[RH_RF95_MAX_MESSAGE_LEN];
char radiopacket[5];



unsigned int unique_id() {
  // read unique CPU Id
  char bufId[33];
  printChipId(bufId);
  unsigned int myId_i = CRC32::calculate(bufId, 32);  // compute checksum
  Serial.print("My id = ");
  Serial.println(myId_i);
  myId_i = myId_i % 1000;
  return myId_i;
}
void radioInit() {
  unsigned int myId_i = unique_id();
  sprintf(myId, "%3d", myId_i);
  radiopacket[1] = myId[0];
  radiopacket[2] = myId[1];
  radiopacket[3] = myId[2];
  radiopacket[4] = 'N';  // isArmed

  Serial.println("CWH Camera Trigger RFM69/RFM95 TXRX!");
  Serial.println();

  // RFM69 Reset pin definition
#if defined(MODULE_RFM69)
  pinMode(RFM69_RST, OUTPUT);
  digitalWrite(RFM69_RST, LOW);

#else
  pinMode(RFM95_RST, OUTPUT);
  digitalWrite(RFM95_RST, HIGH);

#endif

  // manual reset

#if defined(MODULE_RFM69)
  digitalWrite(RFM69_RST, HIGH);
  delay(10);
  digitalWrite(RFM69_RST, LOW);
  delay(10);
  Serial.println("Using module RFM65");
#else
  Serial.println("Using module RFM95");


#endif


  while (!radio_m0.init()) {
    Serial.println("LoRa radio init failed");
    Serial.println("Uncomment '#define SERIAL_DEBUG' in RH_RF95.cpp for detailed debug info");
    while (1)
      ;
  }
  Serial.println("LoRa radio init OK!");

  // Defaults after init are 434.0MHz, modulation GFSK_Rb250Fd250, +13dbM
  if (!radio_m0.setFrequency(FREQ)) {
    Serial.println("setFrequency failed");
    while (1)
      ;
  }
  Serial.print("Set Freq to: ");
  Serial.println(FREQ);



  // If you are using a high power RF69 eg RFM69HW, you *must* set a Tx power with the
  // ishighpowermodule flag set like this:
#if defined(MODULE_RFM69)
  radio_m0.setTxPower(20, true);  // range from 14-20 for power, 2nd arg must be true for 69HCW
#else
  radio_m0.setTxPower(23, false);
#endif




  // The encryption keyhas to be the same as the one in the server
  uint8_t key[] = { 0x01, 0x02, 0x03, 0x04, 0x05, 0x06, 0x07, 0x08,
                    0x01, 0x02, 0x03, 0x04, 0x05, 0x06, 0x07, 0x08 };
#if defined(MODULE_RFM69)
  radio_m0.setEncryptionKey(key);
#else
// no encryption
#endif
}


// state variables for commands received by radio


bool externalSensorCameraOnly = false;


void radioSendPoll() {
  // Poll requeset to destination nodes
  radiopacket[0] = 'P';
  radio_m0.send((uint8_t *)radiopacket, strlen(radiopacket));
  radio_m0.waitPacketSent();
}
void radioSendCameraTrigger() {
  // Trigger destination nodes
  radiopacket[0] = 'T';
  radio_m0.send((uint8_t *)radiopacket, strlen(radiopacket));
  radio_m0.waitPacketSent();
}
void radioSendArmedCommand() {
  radiopacket[0] = 'A';
  radio_m0.send((uint8_t *)radiopacket, strlen(radiopacket));
  radio_m0.waitPacketSent();
}
void radioSendDisarmCommand() {
  radiopacket[0] = 'D';
  radio_m0.send((uint8_t *)radiopacket, strlen(radiopacket));
  radio_m0.waitPacketSent();
}
void radioSendFireCommand() {
  // Trigger destination nodes
  radiopacket[0] = 'F';
  radio_m0.send((uint8_t *)radiopacket, strlen(radiopacket));
  radio_m0.waitPacketSent();
}
void pollResponse() {
  Serial.print("Got an id response back: ");
  Serial.print((char *)buf);
  Serial.print(", RSSI: ");
  Serial.println(radio_m0.lastRssi(), DEC);
  tone(BUZZER_OUT_PIN, 1500 /* hz*/, 100 /* ms */);
}
void radioSendTickleCamera() {
  // Poll requeset to destination nodes
  radiopacket[0] = 'Q';
  radio_m0.send((uint8_t *)radiopacket, strlen(radiopacket));
  radio_m0.waitPacketSent();
}

const unsigned int ARMED_TIMED = 60000;  // 10-15 s // 11/19/23 changed to 60 s
const unsigned int FIRE_TIME = 2000;     // 2 s
const unsigned int POLL_TIME = 200;
const unsigned int POLL_INTERVAL = 3000;

FireTimer armed(ARM_INDICATOR_OUT_PIN, ARMED_TIMED);
FireTimer cameraTrigger(CAMERA_TRIGGER_OUT_PIN, FIRE_TIME);
FireTimer focusTrigger(CAMERA_FOCUS_OUT_PIN, FIRE_TIME);
FireTimer fireRelay(FIRE_INDICATOR_OUT_PIN, FIRE_TIME);
NonBlockingTimer remoteNodeInContact(POLL_INTERVAL);  // fires if poll response received
NonBlockingTimer pollInterval(POLL_INTERVAL);         // sends out a poll request




#if defined(ADAFRUIT_FEATHER_M0)  // Feather M0 w/Radio
//TODO need to check for Adafruit Feather M0
#endif
void setup() {
#ifdef DEBUG
  while (!Serial) {}  // wait for serial port to connect.
#endif
  Wire.begin();

  Serial.begin(19200);

  // output pins
  pinMode(CAMERA_TRIGGER_OUT_PIN, OUTPUT);
  pinMode(CAMERA_FOCUS_OUT_PIN, OUTPUT);
  pinMode(LED_OUT_PIN, OUTPUT);


  // initial output states
  digitalWrite(CAMERA_TRIGGER_OUT_PIN, LOW);
  digitalWrite(CAMERA_FOCUS_OUT_PIN, LOW);
  digitalWrite(LED_OUT_PIN, LOW);


  // input pin assignments for push buttons - reoive

  // 23017 i/o expander
  mcp.init();
  mcp.portMode(MCP23017Port::A, 0);           //Port A as output
  mcp.portMode(MCP23017Port::B, 0b11111111);  //Port B as input

  mcp.writeRegister(MCP23017Register::GPIO_A, 0x00);  //Reset port A
  mcp.writeRegister(MCP23017Register::GPIO_B, 0x00);  //Reset port B

  // Invert inputs (press a button to lit a led (button press gives a "1")
  mcp.writeRegister(MCP23017Register::IPOL_B, 0xFF);
  // Pull up resisters
  mcp.writeRegister(MCP23017Register::GPPU_B, 0b11111111);
  mcp.digitalWrite(RELAY_OUT_PIN, LOW);
  mcp.digitalWrite(ARM_OUT_PIN, LOW);
  mcp.digitalWrite(REMOTE_NODE_IN_CONTACT_LED, LOW);
  Serial.println("mcp init done");

  // init timers
  fireRelay.init();
  armed.init();
  cameraTrigger.init();
  focusTrigger.init();
  remoteNodeInContact.init();
  pollInterval.init();
  pollInterval.check();
  pollInterval.fire();  // send out a poll request;
  Serial.println("Non-blocking timer init done");

  radioInit();
  Serial.println("Radio init done");
  delay(1000);
}

  bool isRadioMode = false;
  bool stateArmSwitch  = false;
  bool stateDisarmSwitch  = false;
  bool fireSwitch  = false;

void loop() {

  // check timers
  armed.check();
  focusTrigger.check();
  cameraTrigger.check();
  fireRelay.check();
  remoteNodeInContact.check();


  // read state of push buttons
  uint8_t io_expander_inputs = mcp.readPort(MCP23017Port::B);
#if DEBUG
  if (io_expander_inputs) {
    Serial.print("MCP input: ");
    Serial.println(io_expander_inputs);
  }
#endif  
  stateArmSwitch = 0x1 & io_expander_inputs;
  stateDisarmSwitch = 0x2 & io_expander_inputs;
  fireSwitch = 0x4 & io_expander_inputs;
  // Setting this - only external sensor will trigger camera
  // (launch fire will not)
  bool externalSensorCameraOnly = 0x8 & io_expander_inputs;

 // Receive commands
  if (radio_m0.available()) {
    stateArmSwitch  = false;
    stateDisarmSwitch  = false;
    fireSwitch  = false;
    
    uint8_t len = sizeof(buf);
    if (radio_m0.recv(buf, &len)) {
      // buf[len] = 0;
      buf[5] = 0;
      char command = buf[0];

#ifdef DEBUG
      Serial.print("Received [");
      Serial.print(len);
      Serial.print("]: ");
      Serial.println((char *)buf);
      Serial.println(command);
      Serial.print("RSSI: ");
      Serial.println(radio_m0.lastRssi(), DEC);
      delay(200);
#endif


      if (strstr((char *)buf, "A")) {
        isRadioMode = true;
        stateArmSwitch = true;

      } else if (strstr((char *)buf, "F")) {
        isRadioMode = true;
        fireSwitch = true;

      } else if (strstr((char *)buf, "D")) {
        isRadioMode = true; 
        stateDisarmSwitch = true;

      
      } else if (strstr((char *)buf, "P")) {  // poll request
        pollResponse();
        remoteNodeInContact.fire();

#if DEBUG
        Serial.println("Received remote poll request");
#endif

} else if (strstr((char *)buf, "T")) {
#if DEBUG
        Serial.println("Got remote trigger");
        delay(1000);
#endif


#if DEBUG
        Serial.println("Recieved camera trigger and remote is set");
#endif

        focusTrigger.fire();
        cameraTrigger.fire();

      } else if (strstr((char *)buf, "R")) {
        // pollResponse();


      }
    }  // end buf size
  }    // end receive command





  // write state of armed switch to LED
  if (stateArmSwitch ) {
    digitalWrite(LED_OUT_PIN, stateArmSwitch);
    Serial.println("Arm swith high");
    delay(100);
  }


  // Read arm switch
  if (stateArmSwitch) {
    armed.fire();
    if(!isRadioMode){
       radioSendArmedCommand();
    }
#if DEBUG
    Serial.println("Setting arm state");
#endif
  }
  if (armed.check()) {
    tone(BUZZER_OUT_PIN, 1000 /* hz*/, 25 /* ms */);
    Serial.println("Armed ...");
  }
  // disarm
  if (stateDisarmSwitch ) {
#if DEBUG
    Serial.println("Clearing Arm state");
#endif

    fireRelay.clear();
    armed.clear();

    // acts as poll
    digitalWrite(CAMERA_TRIGGER_OUT_PIN, HIGH);
    digitalWrite(CAMERA_FOCUS_OUT_PIN, HIGH);


    delay(100);
    digitalWrite(CAMERA_TRIGGER_OUT_PIN, LOW);
    digitalWrite(CAMERA_FOCUS_OUT_PIN, LOW);
    if(!isRadioMode){
      radioSendDisarmCommand();
    }
  }
  //  fire button is  pressed
  if (fireSwitch) {
    
    if (!externalSensorCameraOnly) {
#if DEBUG
      Serial.println("Recieved camera trigger and local is set");
#endif
      focusTrigger.fire();
      cameraTrigger.fire();
    }
    
    
    if (armed.check()) {
      fireRelay.fire();
      if(!isRadioMode){
         radioSendFireCommand();
      }
      armed.clear();
      tone(BUZZER_OUT_PIN, 4000 /* hz*/, 2000 /* ms */);
    }
  }
  // MCP23017 outputs
  if (armed.check()) {
    mcp.digitalWrite(ARM_OUT_PIN, HIGH);
  } else {
    mcp.digitalWrite(ARM_OUT_PIN, LOW);
  }
  if (fireRelay.check()) {
    mcp.digitalWrite(RELAY_OUT_PIN, HIGH);
  } else {
    mcp.digitalWrite(RELAY_OUT_PIN, LOW);
  }
  if (remoteNodeInContact.check()) {
    mcp.digitalWrite(REMOTE_NODE_IN_CONTACT_LED, HIGH);
  } else {
    mcp.digitalWrite(REMOTE_NODE_IN_CONTACT_LED, LOW);
  }
  if (!pollInterval.check()) {
    radioSendPoll();
    pollInterval.fire();
  }


 
#ifdef DEBUG
  delay(500);
#endif
  Serial.println("Loop ...");
  delay(5);
}

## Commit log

2022-07-31 Latest version
    [3178MCU.sch, BLE.sch, Buzzer and Indicators.sch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]
2023-04-02 Adding sensor node pcb files, arduino program, bom, etc.
    [3178MCU.sch, Buzzer and Indicators.sch, CameraTriggerSensorNodeOnly.kicad_pcb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]
2023-06-14 Using the CameraTrig board as a remote launcher.
2023-06-16 JLBPCBfab stuff
    - JLBPCBfab stuff
    - Kicad project for CameraTrig Rev 4_1
    [3178MCU.sch, Buzzer and Indicators.sch, CameraIO.sch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]
2023-06-18 Adding BOM (non JLCPCB parts)
    [Non_JLBPCB_BOM.xlsx]
2023-06-18 Moving files
    [3178MCU.sch, Buzzer and Indicators.sch, CameraIO.sch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]
2023-07-02 Adding 4.2 design Unit tests
    [3178MCU.sch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]
2023-07-02 Removing Rev 4_1 as Rev 4_2 replaces it
    [3178MCU.sch, Buzzer and Indicators.sch, CameraIO.sch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]
2023-07-02 Removing old version
    [4ch Mouser BOM.xlsx]
2023-07-03 Update to Kicad 7
    [3178MCU.kicad_sch, Buzzer and Indicators.kicad_sch, CameraIO.kicad_sch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]
2023-07-04 Adding 4ch relay board
    [4ChWirelessLaunchController.kicad_pcb, 4ChWirelessLaunchController.kicad_sch, file648CD676.kicad_sch]
2023-07-04 Moving some files around
    [CameraTriggerSensorNodeOnly-B_Cu.gbl, CameraTriggerSensorNodeOnly-B_Fab.gbr, CameraTriggerSensorNodeOnly-B_Mask.gbs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]
2023-07-04 Starting to work on RocketTrig_Rev4_2_board_1ch_sw (doesn't work yet)
    [RemoteLaunch_Controller__rev4_2_SW.ino, UT_MCP23017_PortCopyEx.ino, UT_buzzer.ino]
2023-07-05 Adding UT for mcp23017 i/o on rev4_2 board
2023-07-05 Rev4_2 1 ch board works now
2023-07-08 Adding schematics
2023-07-09 Adding Rev4_3
    [3178MCU.kicad_sch, 3178MCU.sch, BOM_non_JLCPCB.xlsx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]
2023-07-10 Adding Rev4_3 rev
    [3178MCU.kicad_sch, BOM_non_JLCPCB.xlsx, Buzzer and Indicators.kicad_sch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]
2023-07-10 Turning off a debug aspect that requires attaching a serial monitor for the program to run
2023-07-11 Fixing glitch in relay board; Sending REv4_3 to fab
    [4ChWirelessLaunchController.kicad_pcb, CameraTriggerSensorNodeOnly.kicad_pcb, JLCPCB Basic SMT Components.xlsx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]
2023-07-21 Printing relay board schematic
2023-11-19 Changing armed time from 10s to 60s; Putting i/o pin for "launch trigger" (default) of cameras, or external sensor
2023-11-24 Adding local/remote; Poll for remote note w/ response to LED
2023-12-21 latest changes
    [4ChWirelessLaunchController.kicad_pcb, CameraTriggerSensorNodeOnly.kicad_pcb, ESP32-S3-MINI-1-N8.step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]
2023-12-23 Works with state machines for mcp commands; relays on remote still sycle frequently - TODO fix this
2023-12-25 Added heartbeats; Buzzer when armed (tx); rx buzzer goes when fired, but TODO needs to be for armed
    [RemoteLaunch_Controller__6ch_sw_RX.ino, RemoteLaunch_Controller__6ch_sw_TX.ino]
2023-12-31 Adding panel diagrams and lightburn files
    [ESP32-S3-MINI-1-N8.step, LowCostRocketTracker.kicad_pcb, LowCostRocketTracker.kicad_sch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]
2024-01-01 Updating hole dims for fuse
2024-01-27 Working on adding polling / heartbeat; Seem to have broken launch
    [3178MCU.kicad_sch, 4ChWirelessLaunchController.kicad_pcb, Buzzer and Indicators.kicad_sch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]
2024-01-30 Removed mcp line that was immediately turning relays off. Yeah! Works now as before.
2024-02-01 Chnge to relay board
    [4ChWirelessLaunchController.sch, 4ch Mouser BOM.xlsx]
2024-07-21 Fixed 1ch 4_3 so that remote sensor will trigger camera in "remote" position
    [RemoteLaunch_Controller__6ch_sw_RX.ino]
2024-07-21 Making remote/local switch for triggering camera. Local will be launch button, remote will be external lsensor
2024-08-05 Major rework to get remote note to work with camera sensor.
    [RemoteLaunch_Controller__rev4_2_SW.ino]
2025-01-12 Update RemoteLaunch_Controller__6ch_sw_RX.ino
    Fixing ch4 so that it stays on for 2 sec ; Manually ported some changes from main
    [RemoteLaunch_Controller__6ch_sw_RX.ino]
